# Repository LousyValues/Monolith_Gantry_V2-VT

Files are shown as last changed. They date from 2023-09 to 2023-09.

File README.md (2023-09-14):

# Monolith Gantry for Voron 2.4 and Trident [BETA]

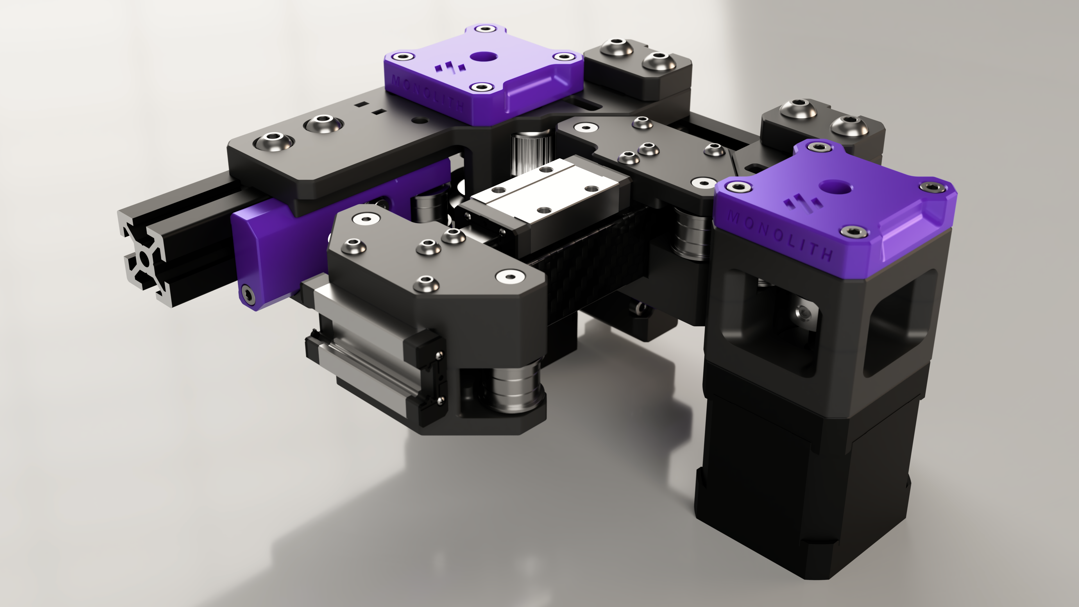
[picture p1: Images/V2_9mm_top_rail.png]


## Updates
### 14.09.2023:

I added the STLs for all of the existing combinations. Huge thanks to ***@krankydonkey*** for remixing all of the Archetype belt clamps for this flipped belt path (CAD/STLs added).
### 11.09.2023:

I added the complete X-axis CAD with motor mount clearances to help with toolhead compatibility checks and XY joint and/or toolhead carriage remixing.

A lot of the usable hardware combinations are also included: pins, standoffs, shoulder bolts, etc.

- **Front rail:** belt location from the X-beam is yet to be decided. I am open to suggestions on how we should make the flipped belt path compatible with existing Voron(mod) toolheads. XY joints CAD available for 6 and 9mm belts.

- **Top rail:** the included VZ-Hevort CNC toolhead compatible 6 and 9mm XY joints are easy to remix for different top rail toolheads. Please make sure the layout matches your toolhead (eg. front right belt is upper or lower). Motor mounts will be compatible with both if they're printed accordingly (normal or mirrored).

## What's this?
This is a performance-oriented, configurable gantry system for Voron 2.4 and Trident. It brings VZbot AWD simplicity and Voron space efficiency together.

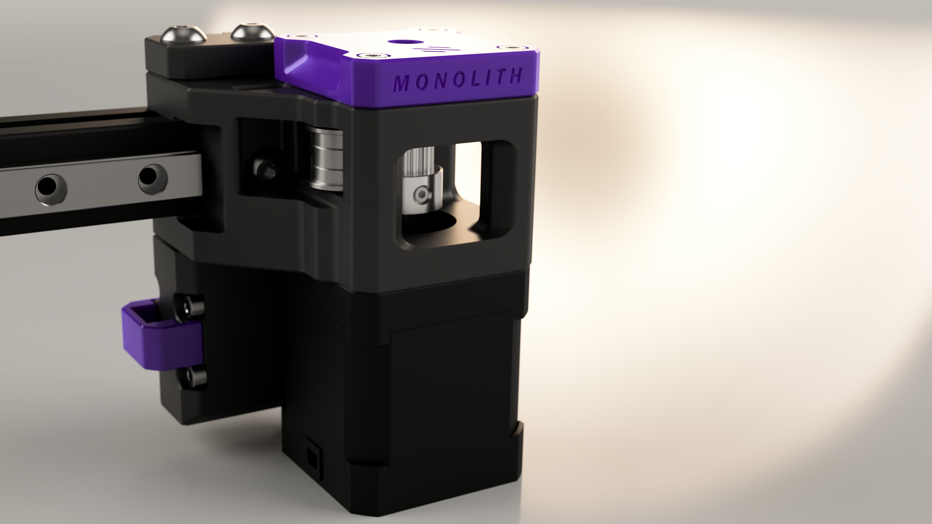
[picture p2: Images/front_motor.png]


**Available gantry configurations:**
- V2 6mm AWD
- V2 9mm AWD
- VT 6mm AWD
- VT 9mm AWD

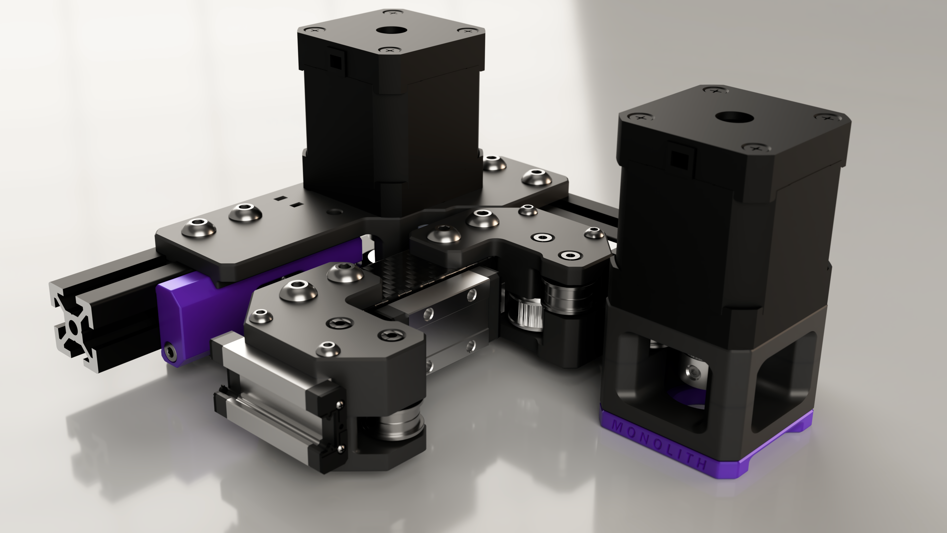
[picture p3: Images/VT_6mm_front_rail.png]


**Available X-axis configurations:**
- Top rail (preferred, no build volume loss with certain toolheads)
- Front rail (flipped belts, toothed side facing the X extrusion)

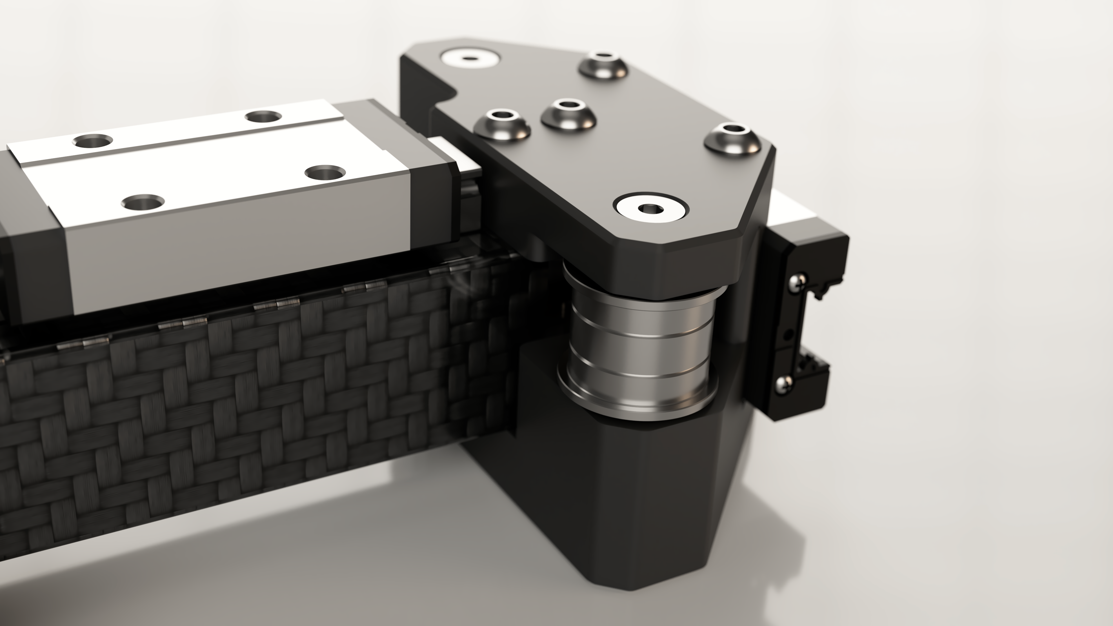
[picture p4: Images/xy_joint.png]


## What's the catch?
You have to space out the front and rear panels on your printer by using 5mm or 2x3mm foam tape.

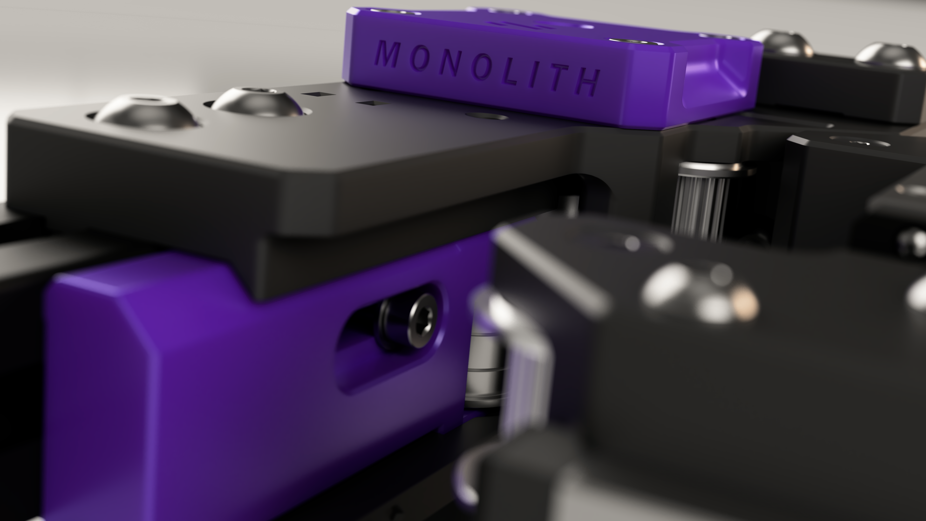
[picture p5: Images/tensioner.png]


## Prerequisites for Monolith AWD
- Z chain relocation on V2
- 5mm or double 3mm foam tape under the rear and the front panels, because there's a 3.6mm stepper protrusion
- OR a 4040 frame
- 9 stepper drivers (or CAN) on V2
- 8 stepper drivers on Trident
- Trident may need a bed relocation to get to the front of the bed (you can just move the PEI sheet for the same effect)
- VZ-Hevort CNC toolhead is recommended for no build volume loss (XY joints already available for 6 and 9mm belts)
- OR any toolhead that you make compatible with this gantry (top rail or flipped belt path front rail)

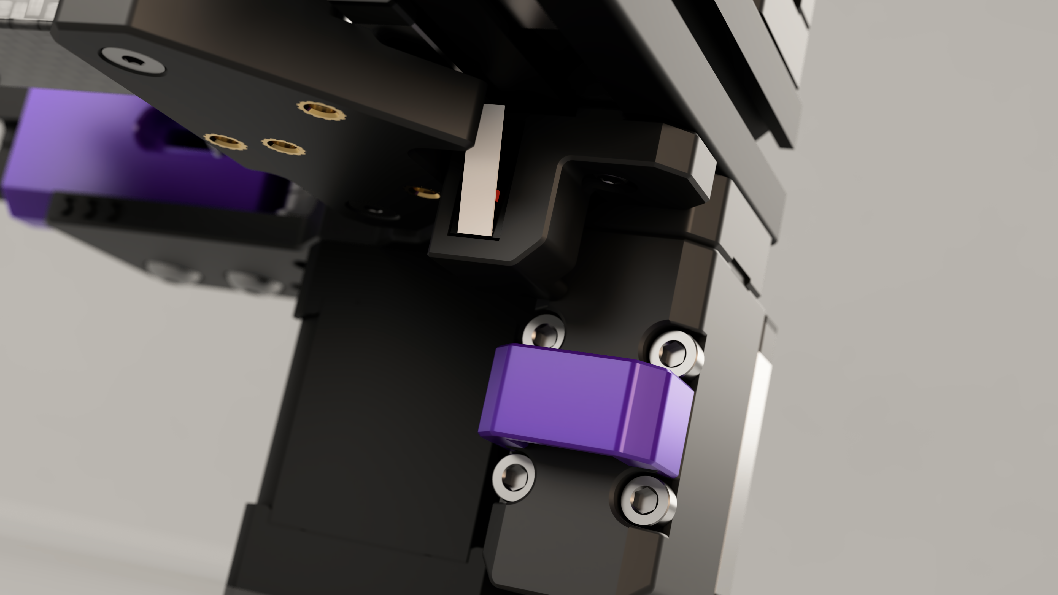
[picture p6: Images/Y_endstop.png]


## BOM
### DISCLAIMER: A lot of this stuff is untested, so the BOM and files will change with more testing and feedback.

To keep the BOM lists relatively simple, I'm going to include all the hardware and motion parts for the motor mounts and XY joints (with the stock stuff included). X extrusion/tube mounting hardware is not included because that can vary based on the configuration.
### Rails:
- **Y rails:** MGN9H
- **X rail:** MGN9H/MGN12H
### X axis:
- **Front rail:** any stock-compatible X beam will work with the suitable mounting hardware (remixed XY joints may be required).
- **Top rail:** any stock-compatible X beam that can be rotated 90 degrees and can accommodate new XY joint holes will work.
### Belts:
If you don't switch belt sizes, the stock length will be enough.
### [V2.4|6mm|AWD] motor mounts and XY joints
|No.|Description|Qty|
|---|---|---|
|1.|NEMA17 motors (preferably identical)|4 pcs|
|2.|6mm GT2 20T drive pulley|4 pcs|
|3.|F695 flanged bearing|12 pcs|
|4.|6mm GT2 20T Idler|4 pcs|
|5.|6mm GATES GT2 belt|stock length|
|6.|Round aluminum M3 standoff 25x5mm (dowel pins or smooth rods will also work)|8 pcs|
|7.|5x20mm dowel pin/smooth rod (round aluminum M3 standoffs 20x5mm will also work)|2 pcs|
|8.|M5 1mm spacer|12 pcs|
|9.|M3x6 BHCS|4 pcs|
|10.|M3x10 BHCS|4 pcs|
|11.|M3x30 BHCS|8 pcs|
|12.|M3x8 FHCS|11 pcs|
|13.|M3x12 SHCS|2 pcs|
|14.|M3x35 SHCS|16 pcs|
|15.|M3x40 SHCS|2 pcs|
|16.|M3 washer (7mm OD max.)|2 pcs|
|17.|M3x5x4mm heatset inserts|10 pcs|
|18.|M5x10 BHCS|8 pcs|
|19.|M5x12 BHCS|4 pcs|
|20.|M5x16 BHCS|8 pcs|
|21.|M3 roll in T-nut|3 pcs|
|22.|M5 roll in T-nut|28 pcs|
|23.|M2 self tapping screw|2 pcs|

### [V2.4|9mm|AWD] motor mounts and XY joints
|No.|Description|Qty|
|---|---|---|
|1.|long shafted (S35/S55/S80) NEMA17 motors (preferably identical)|4 pcs|
|2.|9mm GT2 20T drive pulley|4 pcs|
|3.|F695 flanged bearing|12 pcs|
|4.|695 bearing|10 pcs|
|5.|9mm GT2 20T Idler|4 pcs|
|6.|9mm GATES GT2 belt|stock length|
|7.|Round aluminum M3 standoff 30x5mm (dowel pins or smooth rods will also work)|8 pcs|
|8.|5x20mm dowel pin/smooth rod (round aluminum M3 standoffs 20x5mm will also work)|2 pcs|
|9.|M5 0.5mm spacer|8 pcs|
|10.|M3x6 BHCS|4 pcs|
|11.|M3x10 BHCS|4 pcs|
|12.|M3x35 BHCS|8 pcs|
|13.|M3x8 FHCS|11 pcs|
|14.|M3x12 SHCS|2 pcs|
|15.|M3x45 SHCS|16 pcs|
|16.|M3x40 SHCS|2 pcs|
|17.|M3 washer (7 mm OD max.)|2 pcs|
|18.|M3x5x4 mm heatset inserts|10 pcs|
|19.|M5x12 BHCS|12 pcs|
|20.|M5x20 BHCS|8 pcs|
|21.|M3 roll in T-nut|3 pcs|
|22.|M5 roll in T-nut|28 pcs|
|23.|M2 self tapping screw|2 pcs|
|24.|M5 washer (10mm OD max.)|4 pcs|

### GE5C Z joints (only for 6mm belts)
|No.|Description|Qty|
|---|---|---|
|1.|GE5C bearing|4 pcs|
|2.|M3x16 SHCS|16 pcs|
|3.|M5x16 SHCS|4 pcs|
|4.|M5x20 SHCS|4 pcs|
|5.|M5 1mm spacer|4 pcs|

### Rigid Z joints (6 and 9mm belts)
|No.|Description|Qty|
|---|---|---|
|1.|M3x25 SHCS|16 pcs|
|2.|M5x40 SHCS|8 pcs|

### [VT|6mm|AWD] motor mounts and XY joints
|No.|Description|Qty|
|---|---|---|
|1.|NEMA17 motors (preferably identical)|4 pcs|
|2.|6mm GT2 20T drive pulley|4 pcs|
|3.|F695 flanged bearing|12 pcs|
|4.|6mm GT2 20T Idler|4 pcs|
|5.|6mm GATES GT2 belt|stock length|
|6.|Round aluminum M3 standoff 25x5mm (dowel pins or smooth rods will also work)|8 pcs|
|7.|5x20mm dowel pin/smooth rod (round aluminum M3 standoffs 20x5mm will also work)|2 pcs|
|8.|M5 1mm spacer|16 pcs|
|9.|M3x6 BHCS|4 pcs|
|10.|M3x10 BHCS|4 pcs|
|11.|M3x30 BHCS|8 pcs|
|12.|M3x8 FHCS|11 pcs|
|13.|M3x12 SHCS|2 pcs|
|14.|M3x35 SHCS|16 pcs|
|15.|M3x40 SHCS|2 pcs|
|16.|M3 washer (7mm OD max.)|2 pcs|
|17.|M3x5x4mm heatset inserts| 10 pcs|
|18.|M5x10 BHCS|24 pcs|
|19.|M5x12 BHCS|8 pcs|
|20.|M3 roll in T-nut|3 pcs|
|21.|M5 roll in T-nut|32 pcs|
|22.|M2 self tapping screw|2 pcs|

### [VT|9mm|AWD] motor mounts and XY joints
|No.|Description|Qty|
|---|---|---|
|1.|long shafted (S35/S55/S80) NEMA17 motors (preferably identical)|4 pcs|
|2.|9mm GT2 20T drive pulley|4 pcs|
|3.|F695 flanged bearing|12 pcs|
|4.|695 bearing|10 pcs|
|5.|9mm GT2 20T Idler|4 pcs|
|6.|9mm GATES GT2 belt|stock length|
|7.|Round aluminum M3 standoff 30x5mm (dowel pins or smooth rods will also work)|8 pcs|
|8.|5x20mm dowel pin/smooth rod (round aluminum M3 standoffs 20x5mm will also work)|2 pcs|
|9.|M5 0.5mm spacer|8 pcs|
|10.|M3x6 BHCS|4 pcs|
|11.|M3x10 BHCS|4 pcs|
|12.|M3x35 BHCS|8 pcs|
|13.|M3x8 FHCS|11 pcs|
|14.|M3x12 SHCS|2 pcs|
|15.|M3x45 SHCS|16 pcs|
|16.|M3x40 SHCS|2 pcs|
|17.|M3 washer (7 mm OD max.)|2 pcs|
|18.|M3x5x4 mm heatset inserts| 10 pcs|
|19.|M5x12 BHCS|32 pcs|
|20.|M3 roll in T-nut|3 pcs|
|21.|M5 roll in T-nut|32 pcs|
|22.|M2 self tapping screw|2 pcs|
|23.|M5 washer (10mm OD max.)|8 pcs|

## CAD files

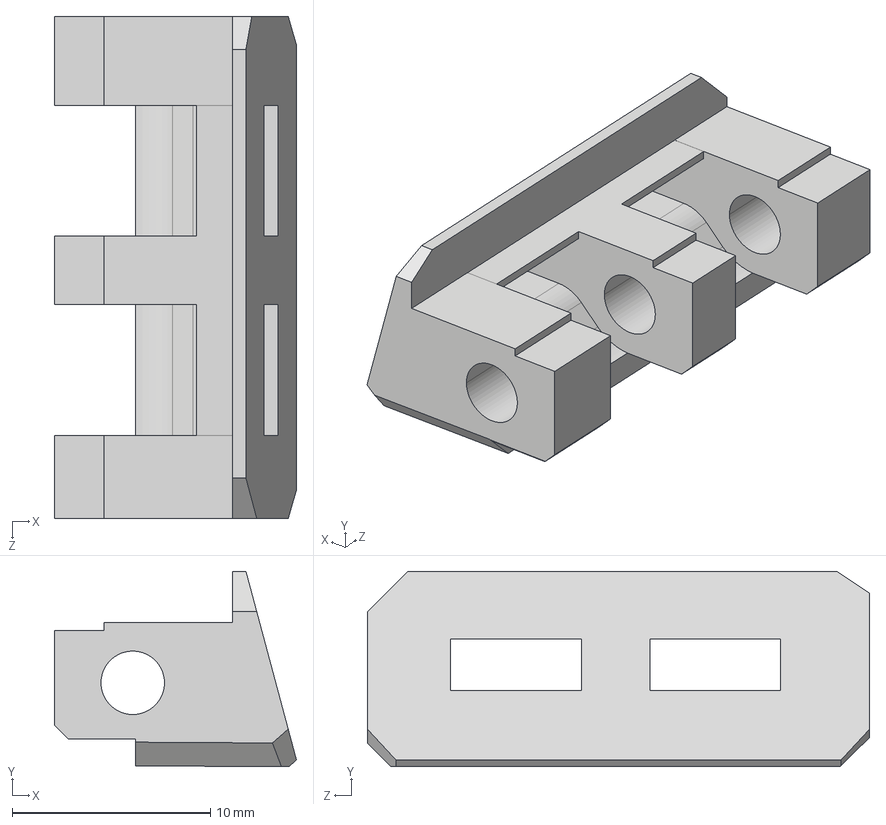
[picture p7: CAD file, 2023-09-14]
CAD/Archetype_belt_clips/MGN12/Archetype_RailMount_MGN12-6mm_LOOSE(EPDM)_Clampx2.STEP
12.2 x 9.86 x 25.3 mm

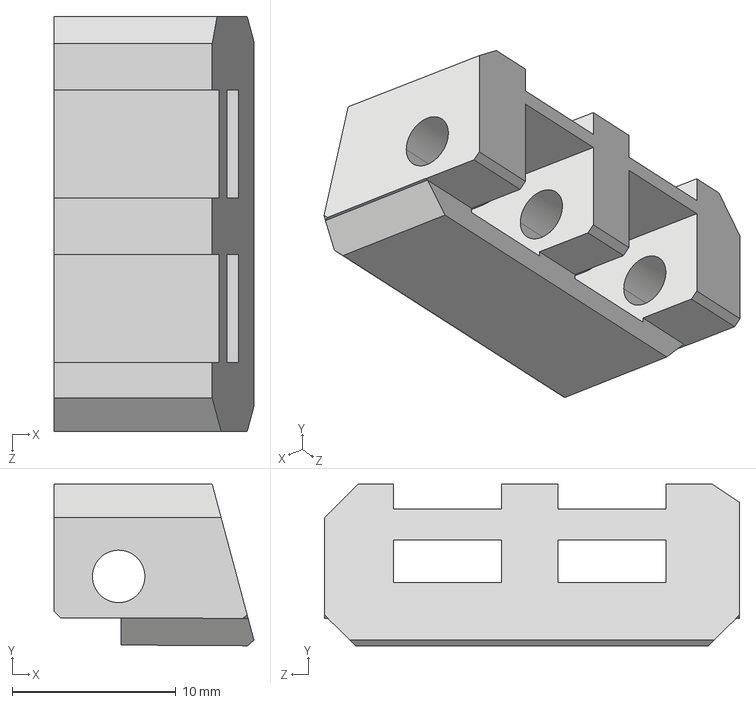
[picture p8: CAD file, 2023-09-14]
CAD/Archetype_belt_clips/MGN9/Archetype_RailMount_MGN9-6mm_LOOSE(EPDM)_Clampx2.STEP
12.2 x 9.86 x 25.3 mm

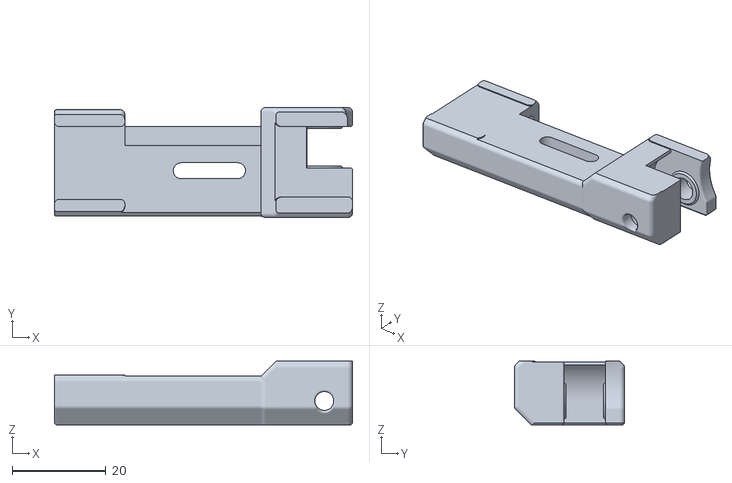
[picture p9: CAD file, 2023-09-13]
STLs/6mm_belts/[a]_6mm_tensioner_x2.stl
63.5 x 23.5 x 13.6

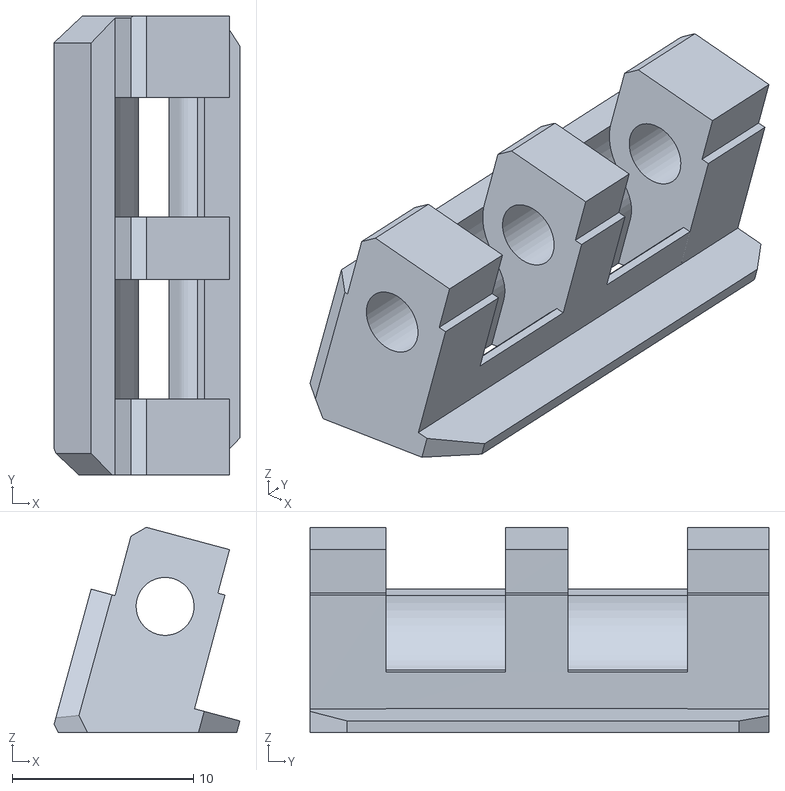
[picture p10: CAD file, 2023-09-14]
STLs/6mm_belts/Archetype_belt_clips_6mm/MGN12/Archetype_RailMount_MGN12-6mm_TIGHT(STANDARD)_Clampx2.STL
10.3 x 25.3 x 11.3

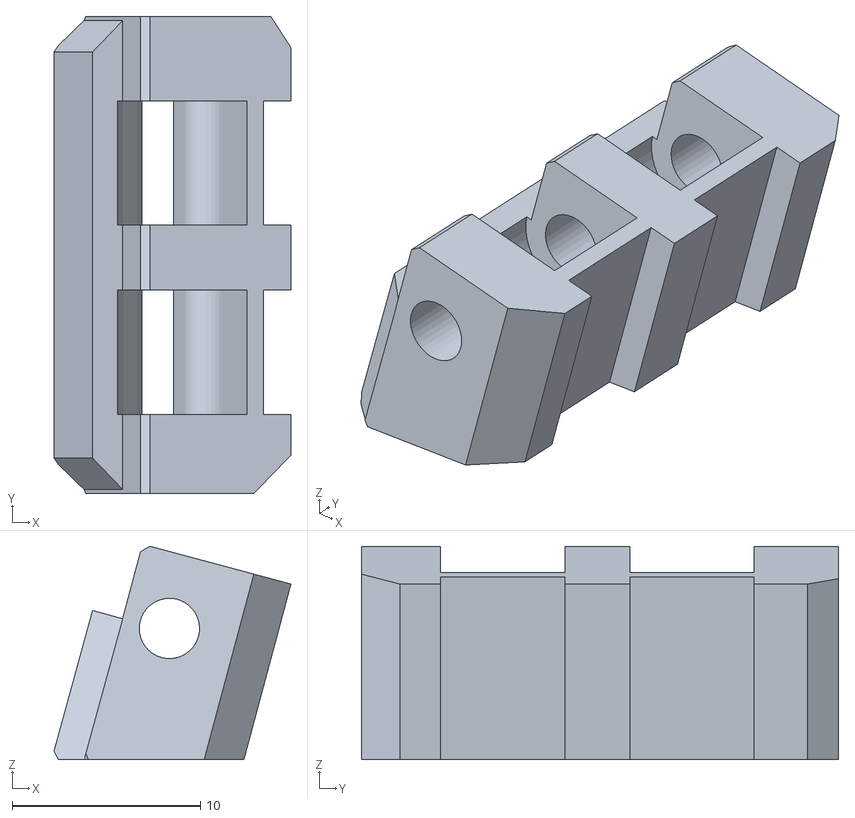
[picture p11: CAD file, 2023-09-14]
STLs/6mm_belts/Archetype_belt_clips_6mm/MGN9/Archetype_RailMount_MGN9-6mm_TIGHT(STANDARD)_Clampx2.STL
12.6 x 25.3 x 11.3

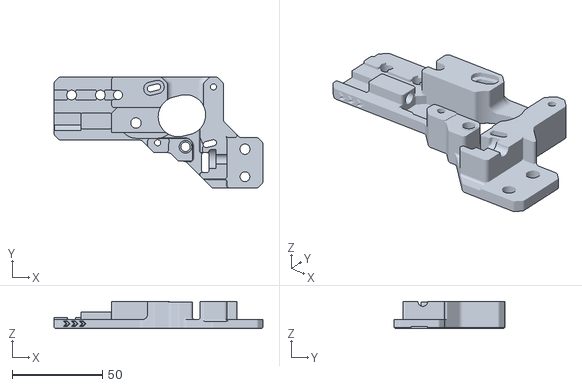
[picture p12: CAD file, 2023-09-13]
STLs/6mm_belts/V2_6mm/V2_6mm_rear_motor_mount_body_b_x2.stl
116.0 x 61.6 x 15.0

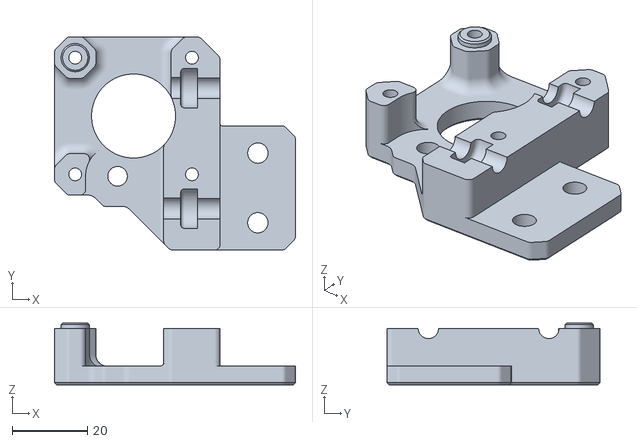
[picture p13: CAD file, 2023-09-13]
STLs/6mm_belts/VT_6mm/VT_6mm_front_motor_mount_body_a_x2.stl
64.0 x 56.6 x 16.4

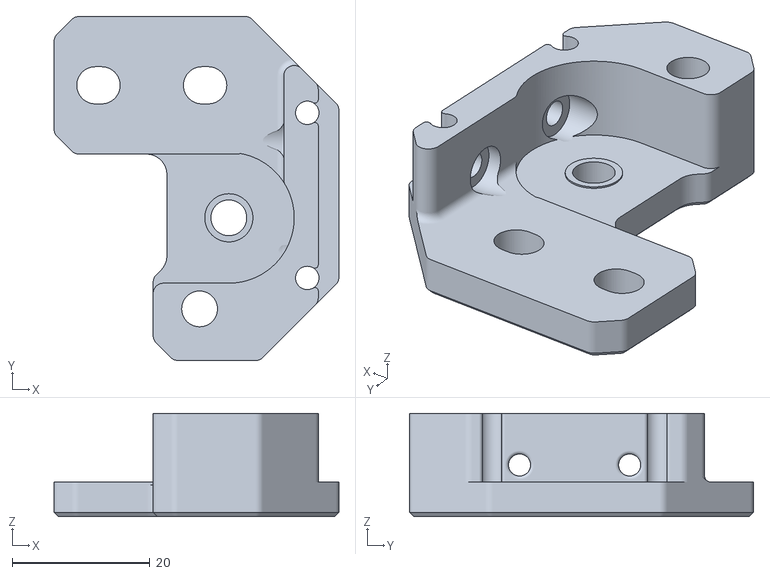
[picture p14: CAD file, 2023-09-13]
STLs/6mm_belts/XY_joints_6mm/6mm_Front_rail/6mm_Experimental_Archetype_XY_joints/6mm_Archetype_XY_joint_left_upper.stl
41.4 x 50.0 x 15.0

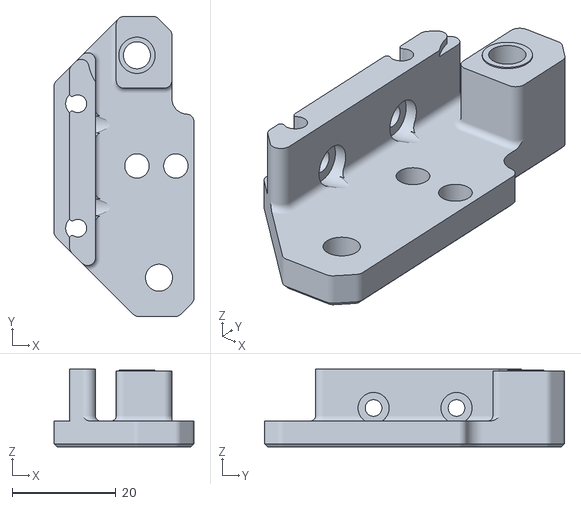
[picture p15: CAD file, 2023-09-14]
STLs/6mm_belts/XY_joints_6mm/6mm_Top_rail/6mm_VZ-Hevort_XY_joints/6mm_VZ_Hevort_XY_joint_left_lower.stl
27.0 x 57.9 x 15.0

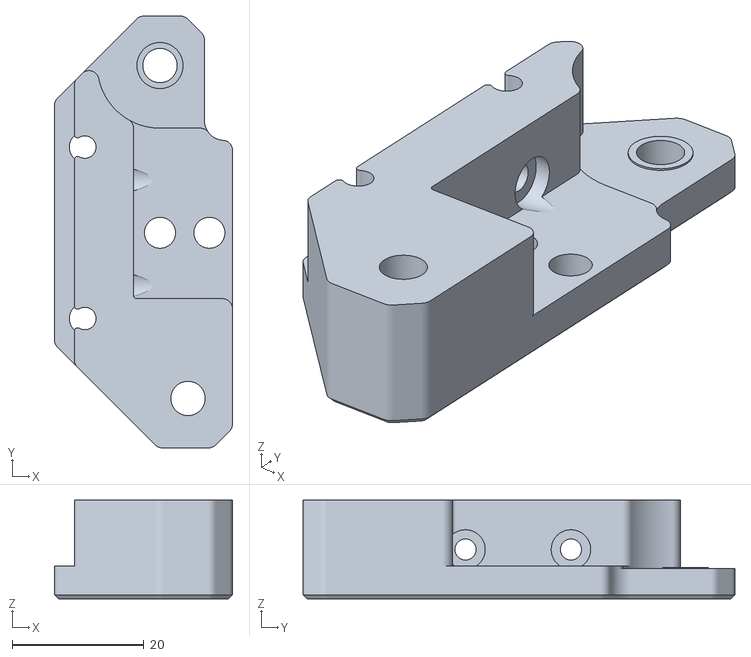
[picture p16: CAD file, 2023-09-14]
STLs/6mm_belts/XY_joints_6mm/6mm_Top_rail/6mm_VZ_spacing_XY_joints/FOR_MIRRORED_GANTRY_6mm_VZ_spacing_XY_joint_left_lower.stl
27.0 x 65.5 x 15.0

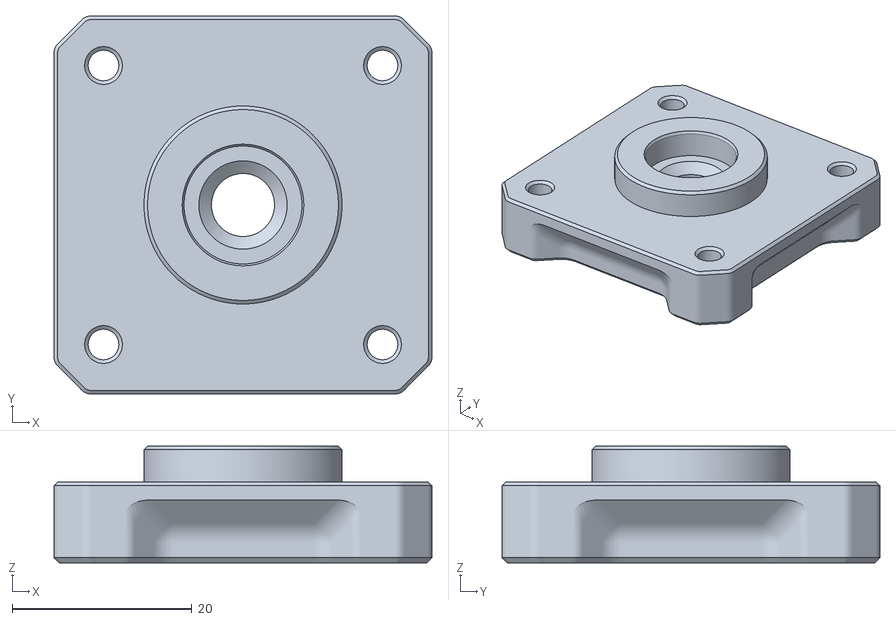
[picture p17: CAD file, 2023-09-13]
STLs/9mm_belts/[a]_9mm_support_bearing_housing_flipped_x4.stl
42.0 x 42.0 x 13.0

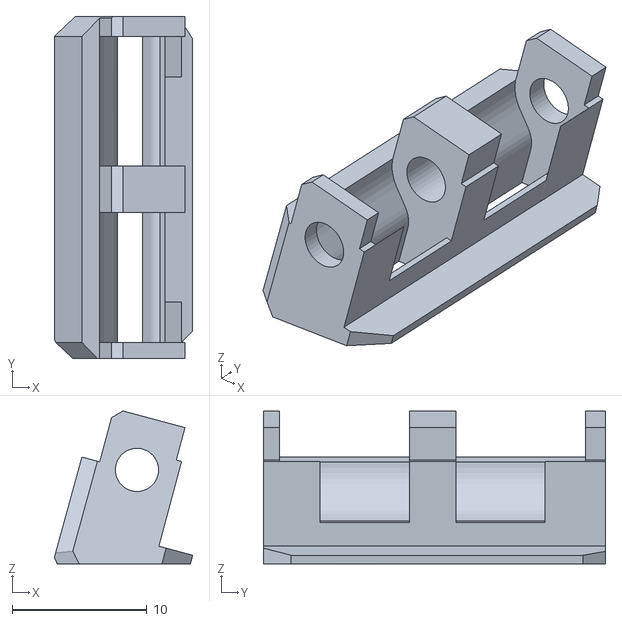
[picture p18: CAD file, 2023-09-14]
STLs/9mm_belts/Archetype_belt_clips_9mm/MGN12/Archetype_RailMount_MGN12-9mm_LOOSE(EPDM)_Clampx2.STL
10.3 x 25.3 x 11.3

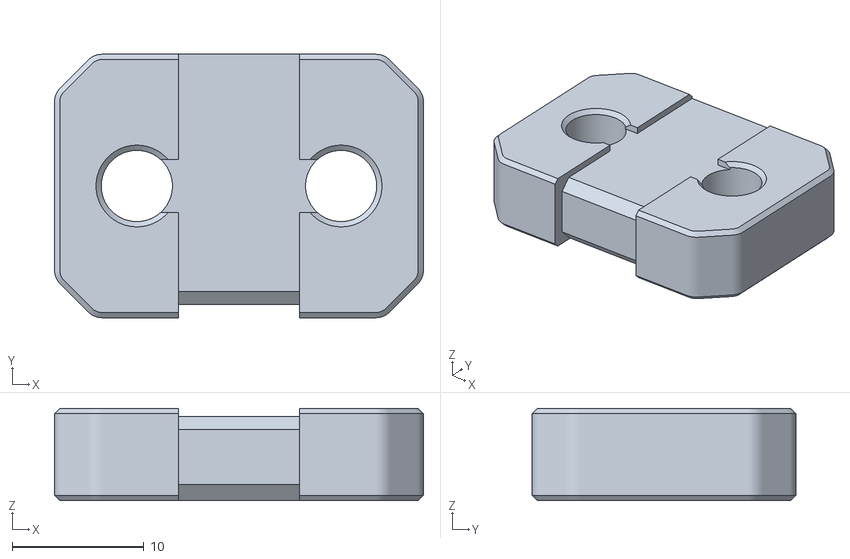
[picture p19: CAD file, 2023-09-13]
STLs/9mm_belts/V2/9mm_top_z_belt_clamp_x4.stl
28.0 x 20.0 x 7.00

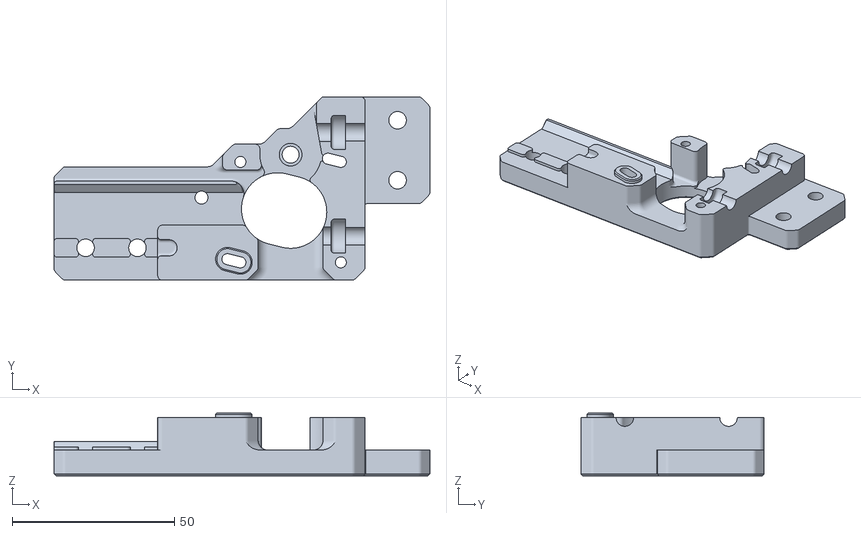
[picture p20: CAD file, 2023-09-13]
STLs/9mm_belts/VT/VT_9mm_rear_motor_mount_body_a_x2.stl
116.0 x 56.6 x 19.4

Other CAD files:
STLs/9mm_belts/Archetype_belt_clips_9mm/MGN9/Archetype_RailMount_MGN9-9mm_LOOSE(EPDM)_Clampx2.STL
STLs/9mm_belts/XY_joints/Front_rail/9mm_Experimental_Archetype_XY_joints/9mm_Archetype_XY_joint_left upper.stl
STLs/9mm_belts/XY_joints/Top_rail/9mm_VZ-Hevort_XY_joints/9mm_VZ_Hevort_XY_joint_left_lower.stl
STLs/Y_endstop_housing.stl
CAD/Archetype_belt_clips/MGN12/Archetype_RailMount_MGN12-6mm_TIGHT(STANDARD)_Clampx2.STEP
CAD/Archetype_belt_clips/MGN12/Archetype_RailMount_MGN12-9mm_LOOSE(EPDM)_Clampx2.STEP
CAD/Archetype_belt_clips/MGN12/Archetype_RailMount_MGN12-9mm_TIGHT(STANDARD)_Clampx2.STEP
CAD/Archetype_belt_clips/MGN9/Archetype_RailMount_MGN9-6mm_TIGHT(STANDARD)_Clampx2.STEP
CAD/Archetype_belt_clips/MGN9/Archetype_RailMount_MGN9-9mm_LOOSE(EPDM)_Clampx2.STEP
CAD/Archetype_belt_clips/MGN9/Archetype_RailMount_MGN9-9mm_TIGHT(STANDARD)_Clampx2.STEP
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

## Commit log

2023-09-08 Added folder
    [9mm_rigid_z_joint_body_x4.stl, [a]_z_joint_cable clip_x4.stl]
2023-09-08 removed test files
    [9mm_rigid_z_joint_body_x4.stl, [a]_z_joint_cable clip_x4.stl]
2023-09-09 BOM test
2023-09-11 Added X-axis CAD and more info
2023-09-11 6mm front rail printed parts clearance fix
2023-09-13 STL added
    [6mm_Archetype_XY_joint_left_lower.stl, 6mm_Archetype_XY_joint_right_lower.stl, 6mm_Archetype_XY_joint_right_upper.stl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]
2023-09-14 only for MIRRORED motor mounts and tensioners
    [6mm_VZ_spacing_XY_joint_left_lower.stl, 6mm_VZ_spacing_XY_joint_left_upper.stl, 6mm_VZ_spacing_XY_joint_right_lower.stl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]
2023-09-14 XY joints for standard VZ toolheads added
    [FOR_MIRRORED_GANTRY_6mm_VZ_spacing_XY_joint_left_lower.stl, FOR_MIRRORED_GANTRY_6mm_VZ_spacing_XY_joint_left_upper.stl, FOR_MIRRORED_GANTRY_6mm_VZ_spacing_XY_j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]
2023-09-14 minor fixes
    [6mm_VZ_Hevort_XY_joint_left_lower.stl, 6mm_VZ_Hevort_XY_joint_left_upper.stl, 6mm_VZ_Hevort_XY_joint_right_lower.stl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]
2023-09-14 Updated X-axis CAD with new configs
2023-09-14 Added remixed Archetype belt clips CAD/STLs
    [Archetype_RailMount_MGN12-6mm_LOOSE(EPDM)_Clampx2.STEP, Archetype_RailMount_MGN12-6mm_LOOSE(EPDM)_Clampx2.STL, Archetype_RailMount_MGN12-6mm_TIGHT(STANDARD)_Cl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]
2023-09-14 9mm BOM and updates
2023-09-14 Orientation fixed
    [Archetype_RailMount_MGN12-6mm_LOOSE(EPDM)_Clampx2.STL, Archetype_RailMount_MGN12-6mm_TIGHT(STANDARD)_Clampx2.STL, Archetype_RailMount_MGN12-9mm_LOOSE(EPDM)_Cla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]
2023-09-27 fixed a clearance issue
    [Y_endstop_housing.stl]
